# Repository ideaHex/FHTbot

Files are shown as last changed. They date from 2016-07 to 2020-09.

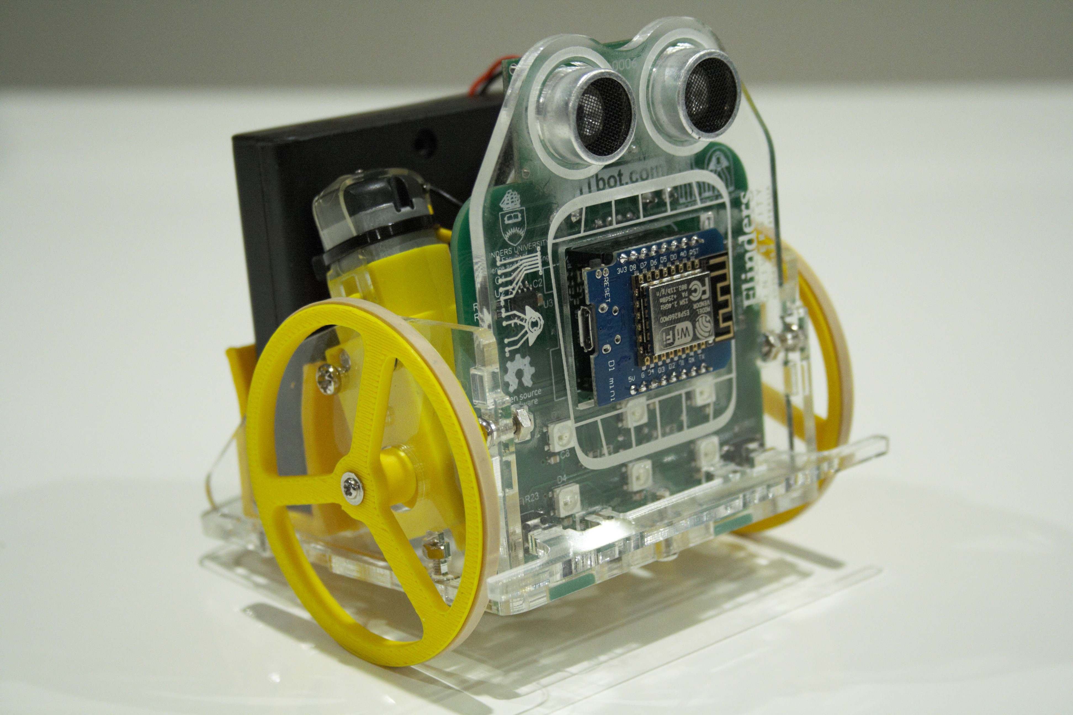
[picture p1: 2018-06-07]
FHTbot HiRes.jpg

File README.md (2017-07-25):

# FHTbot
Firmware for Makerfaire robot
<html>
  <head>

  </head>
  <body>
    <div>
      <h1><span><font face="Comic Sans MS">About</font></span></h1>
      <h3><span><br>The FHTbot was created as a result of a joint effort between Hackerspace Adelaide and Flinders University as an educational tool to provide insights into the following.<br>
<h2><span>The internet of things.</span></h2>
<ul>
  <li><span>Showing how a device can be easily set up as a secure WIFI Hotspot.</span></li>
  <li><span>Allowing most major web browsers to connect and control a real world device and take real time control over it, without the need to install 3rd party applications on the device.</span></li></ul>
<h2><span>Basic robotics.</span></h2>
<ul><li><span>Control motors.</span></li>
<li><span>Using sensors to perceive the world around it.</span></li>
<li><span>Provide visual, auditory, temperature and web client feedback.</span></li>
<li><span>A control system to give the FHTbot basic and complicated commands to perform tasks.</span></li></ul>
<h2><span>Education</span></h2><ul><li><span>
Geometry based navigation system allows students to control the FHTbot and see the FHTbot turn to the angle and proceed to the destination, put simply if you tell the but to turn right 90 degrees it will turn right, turning 180 degrees will turn and face the opposite direction.</span></li></ul>
<h2><span>Fun</span></h2><ul>
<li><span>The FHTbot was designed to be able to be driven like a remote control car.</span></li>
<li><span>The FHTbot was designed to accept a pre - programmed course.</span></li>
<li><span>The FHTbot has an assisted drive mode to help young and inexperienced drivers.</span></li></ul>
<h2><span>We all hope you have as much fun with this FHTbot as we did designing it for you.</span></h2></span></h3>
    </div>
    <br><br>
</body>
</html>

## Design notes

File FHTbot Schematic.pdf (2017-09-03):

# RIGHT_SW VCC

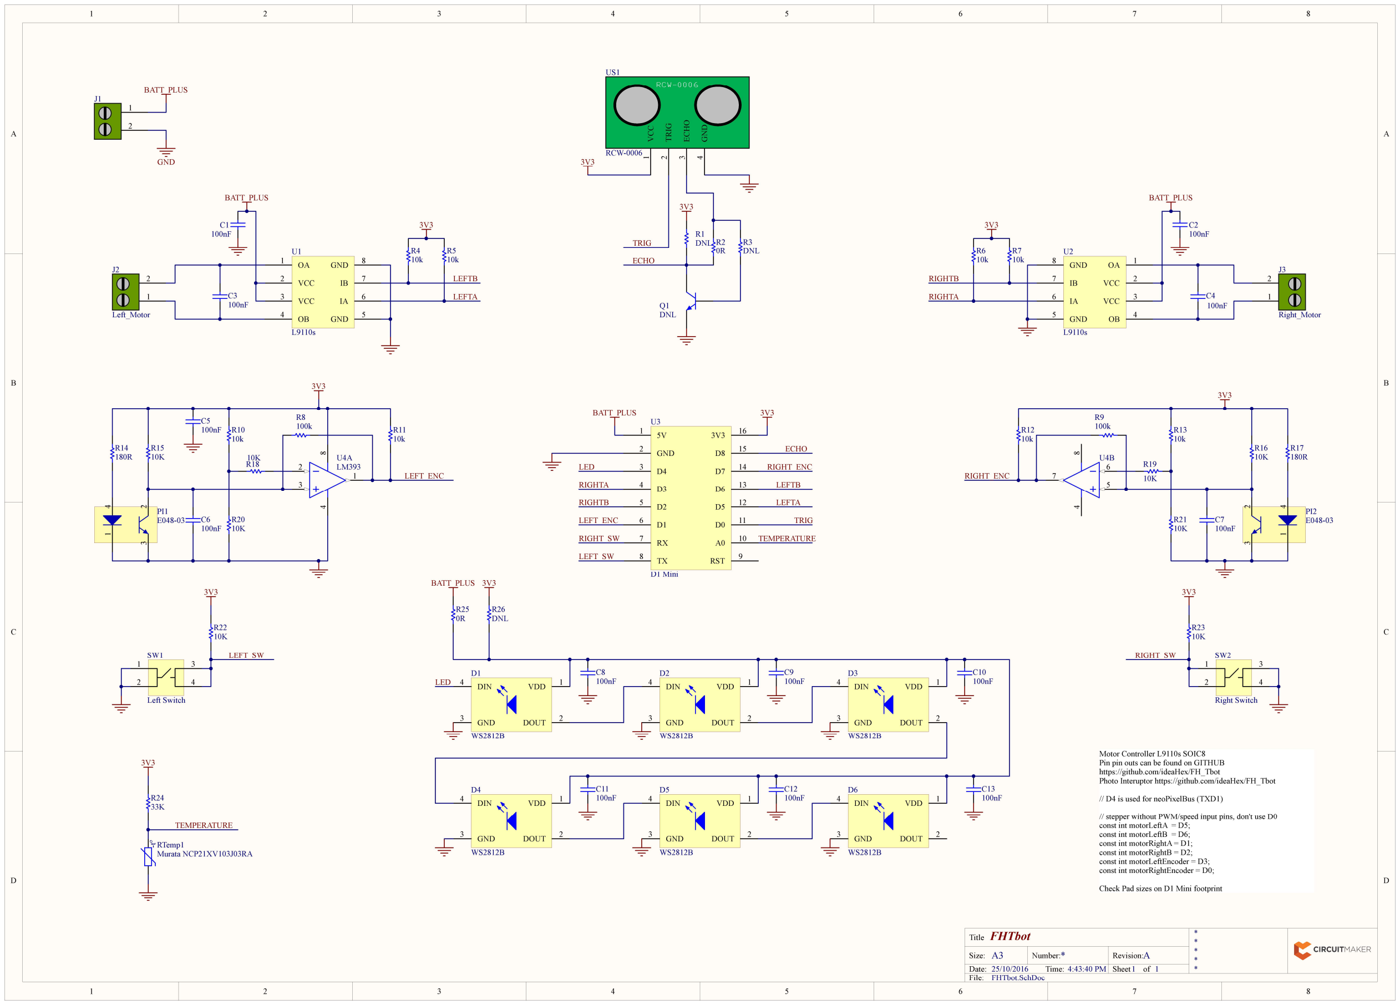
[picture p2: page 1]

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
## FHTbot

* | A
25/10/2016 | 4:43:40 PM
FHTbot.SchDoc

Title

Size: | Number:
Date:
File:

Revision:
Time: | Sheet | of

A3

VDD | 1
DOUT | 2 GND 3

DIN 4

D5

WS2812B

VDD | 1
DOUT | 2 GND 3

DIN 4

D4

WS2812B

VDD | 1
DOUT | 2 GND 3

DIN 4

D6

WS2812B

VDD | 1
DOUT | 2 GND 3

DIN 4

D3

WS2812B

VDD | 1
DOUT | 2 GND 3

DIN 4

D2

WS2812B

VDD | 1
DOUT | 2 GND 3

DIN 4

D1

WS2812B

1

2

J1

1

2

J2

Left_Motor

1

2

J3

Right_Motor

BATT_PLUS

GND

BATT_PLUS

3

2

### 1 ⁸ 4

U4A
LM393

5

6

7 8 4
U4B

R14
180R

R10
10k

R20
10K

3V3

C6
100nF

100nF

C3

C5
100nF

C8
100nF

C9
100nF

C10
100nF

C13
100nF

C12
100nF

C11
100nF

R8
100k
BATT_PLUS | 3V3

Motor Controller L9110s SOIC8
Pin pin outs can be found on GITHUB https://github.com/ideaHex/FH_Tbot
Photo Interuptor https://github.com/ideaHex/FH_Tbot

// D4 is used for neoPixelBus (TXD1)

// stepper without PWM/speed input pins, don't use D0 const int motorLeftA = D5;
const int motorLeftB = D6;
const int motorRightA = D1;
const int motorRightB = D2;
const int motorLeftEncoder = D3; const int motorRightEncoder = D0;

Check Pad sizes on D1 Mini footprint

OA | 1
VCC | 2
VCC | 3
OB | 4 GND 5

IA 6

IB 7

GND 8

U2

L9110s

OA 1

VCC 2

VCC 3

OB 4 | GND | 5
| IA | 6
| IB | 7
GND | 8

U1

L9110s

C1
100nF
BATT_PLUS | BATT_PLUS
| C2 100nF

100nF

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
Left Switch

1

2 4

3

SW2

Right Switch

R17
180R

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
100nF

R9
100k

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
3V3 | 3V3

LED

LED

3V3 | 3V3
RIGHTA | LEFTB

LEFT_ENC

LEFT_ENC

RIGHT_ENC

ECHO

TRIG

ECHO

TRIG

RIGHT_ENC

LEFT_SW | RIGHT_SW -tº RTemp1

Murata NCP21XV103J03RA

R24
33K

3V3

TEMPERATURE

TEMPERATURE

LEFTA

LEFTB

RIGHTA

RIGHTB

RIGHTB | LEFTA

R15
10K

5V 1

GND 2

D4 3

D3 4

D2 5

D1 6

RX 7

TX 8 | RST | 9
| A0 | 10
D0 | 11
D5 | 12
D6 | 13
D7 | 14
D8 | 15
3V3 | 16

U3

D1 Mini

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
LEFT_SW

### 1 TRIG

### 2 ECHO 3 GND

4

RCW-0006

US1

RCW-0006 3 2 1 4 | PI1
E048-03 | 3 2 | 1 4
PI2
E048-03

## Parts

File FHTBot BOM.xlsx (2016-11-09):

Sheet: BOM
Purchased Parts
Qty | Item | Description
2 | Motors | 48:1 Gear motor
2 | Wire | Yellow wire xx mm long
2 | Wire | White wire xx mm long
2 | Cable tie | Cable tie 100mm x 2.5mm
1 | Battery Box | Battery box for 3 x AA battery with switch
3 | Battery | AA battery
1 | Processor | WEMOS D1 mini breakout board for ESP8266EX
1 | Main Board | Assembled FHTBot PCB (see FHTBot PCB BOM for details)
1 | Ultrasonic sensor | RCW0006 Ultrasonic distance sensor, 3V compatible
1 | Velcro | 15cm Self adhesive Velcro strip
2 | Tyres | Size 63 Rubber bands
1 | Castor | M3 Dome nut
1 | Screw for castor | M3 x 6 pan screw
4 | Screw for Motors | M3 x 25 Screw
7 | Screws for Chassis | M3 x 10 Screw
11 | Nuts | M3 Hex nut
4 | Screws for wheels & Encoders | Self Tapping Machine Screw M2.3x6mm Phillip head W/Shoulder
3D Printed Parts
Qty | Item | Description
2 | Wheels | 3D Printed wheels (Wheel.stl)
Laser Cut Parts
Qty | Item | Description
2 | Side | 3 mm thick Clear Acrylic (Side v23.dxf)
1 | Base | 3 mm thick Clear Acrylic (Base v19.dxf)
1 | Front | 3 mm thick Clear Acrylic (Front v37.dxf)
2 | Encoder Spaces | 6 mm thick Acrylic (EncoderSpacer v6.dxf) or 4 @ 3mm thick
2 | Encoders | 3 mm thick Black Acrylic (EncoderWheel v15.dxf)
1 | Bumper | 3 mm thick Clear Acrylic (Bumper v17.dxf)

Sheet: PCB BOM
Designator | Qty | Description | Footprint
J1, J2, J3 | 3 | Screw Terminal
C1, C2, C3, C4, C5, C6, C7, C8, C9, C10, C11, C12, C13 | 13 | 100nF Capacitor | 0805
U1, U2 | 2 | L9110s Motor Controller IC | SOIC-8
R1, R3, R26 | 0 | Do Not Load | 0805
R2, R25, | 2 | 0R Resistor | 0805
R4, R5, R6, R7, R10, R11, R12, R13, R15, R16, R18, R19, R20, R21, R22, R23, R34 | 17 | 10K Resistor | 0805
R14, R17 | 2 | 180R Resistor | 0805
R8, R9 | 2 | 100k Resistor | 0805
RTemp1 | 1 | 33k Resistor | 0805
U3 | 1 | WEMOS D1 Mini
U4 | 1 | LM393 Comparator IC | SOIC-8
US1 | 1 | Header Female RA 4-way
Q1 | 0 | Do Not Load
PI1, PI2 | 2 | E048-03 Photo-interruptor
SW1, SW2 | 2 | Tactile Switch | 6mm x 6mm
D1, D2, D3, D4, D5, D6 | 6 | WS21182 RGB LED

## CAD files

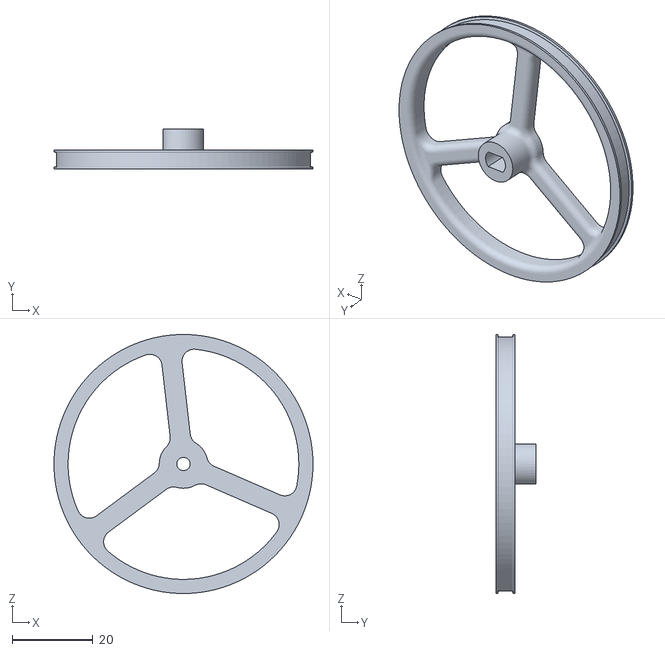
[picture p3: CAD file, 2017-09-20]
Wheel Up.stl
64.0 x 10.0 x 64.0

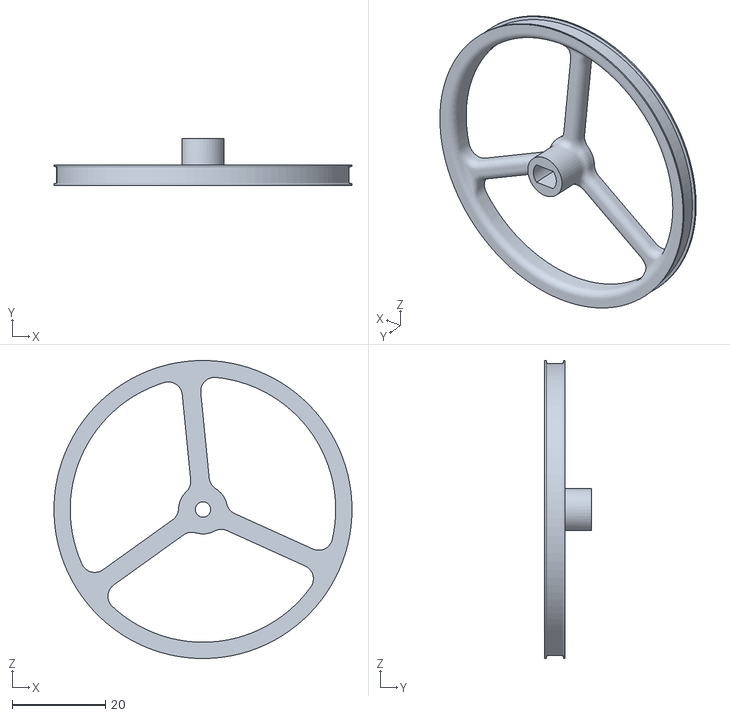
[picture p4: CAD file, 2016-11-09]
Wheel.stl
64.0 x 10.0 x 64.0

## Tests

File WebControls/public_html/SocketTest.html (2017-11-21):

# FHTbot

Touch the screen and move - works with mouse too

__ �C | | ____mm

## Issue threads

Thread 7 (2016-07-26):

Test Issue

ideaHex, 2016-07-26:
Hello World!

TildenG, 2016-07-26:
Looks good

TildenG, 2016-07-26:
I just remembered the standard ping sensor won't work consistently under 5V, I found this out the hard way !. Is there a 3.3V version ?

TildenG, 2016-07-29:
I found a mention on a blog that said that the "HC-SR04+" is a 3.3V version, however I can't find any.

ideaHex, 2016-07-29:
I purchased a IR obstacle sensor from Jaycar tonight so I will play with that as well.

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

TildenG, 2016-07-31:
I've been writing my own ping routines because I'm not happy with the slow inaccurate output from most libraries, I found that my sensor only worked when I connected the echo and trigger together on the 3.3V side of the level converter.
So far I get mm accurate results at 100 pings a second without blocking or oversampling :) .

/*
 * This is a non blocking ping example for the ESP8266 it is capable of 100 pings
 * a second with millimeter accuracy without oversampling.
 *
 * The documentation recommends not pinging faster the 60ms to avoid echo's creating
 * false readings, however I have tested at 10ms at close range (<200mm) without problems
 *
 * Trigger and echo pins need to be tied together on LV side of level converter.
 */

#define TRIGGER D6                                            // Trigger pin
volatile long pingTime;                                       // time taken to complete ping in uS
volatile int distance = -1;                                   // distance in mm

#define MAX_TEST_DISTANCE 5000                                 // in mm
byte maxTimeNeeded = (MAX_TEST_DISTANCE / 10.0 * 58) / 1000;   // in ms
unsigned long previousMillis = millis();                       // used for timeout for no ping received
byte minimumDelay = 10;                                        // to prevent false echo's

void setup() {
  Serial.begin (115200);
  pinMode(TRIGGER, OUTPUT);
}

void loop() {
    getDistance();
}

void startup(){               // ready now, wait for distance
  previousMillis = millis();
  pingTime = micros();
  detachInterrupt(TRIGGER);
  attachInterrupt(TRIGGER, calculateDistance, FALLING);
}
void calculateDistance(){
  long duration = micros() - pingTime + 50;  // added 50 uS to calibrate sensor
  distance = (duration/2.0) / 29.1 * 10.0;
 // distance = (max((duration + 57 / 2) / 57, (duration ? 1 : 0)));
}
void triggerPing(){
  detachInterrupt(TRIGGER);
  pinMode(TRIGGER, OUTPUT);

  digitalWrite(TRIGGER, LOW);         // start low
  delayMicroseconds(2);

  digitalWrite(TRIGGER, HIGH);        // datasheet states a uS 10  pulse to start
  delayMicroseconds(10);

  digitalWrite(TRIGGER, LOW);
  pinMode(TRIGGER, INPUT);            // set input to output so only 1 pin is needed

  attachInterrupt(TRIGGER, startup, RISING);
}

int getDistance(){                   // returns distance or -1 if not available
  if (distance != -1 && millis() - previousMillis > minimumDelay){
      Serial.printf("Distance: %d mm \r\n", distance);
      distance = -1;
      triggerPing();
    }

    if (millis() - previousMillis > maxTimeNeeded){
      previousMillis = millis();    // to stop false starts
      distance = -1;
      triggerPing();
    }
    return distance;
}

TildenG, 2016-08-03:
It would appear that if an hardware interrupt is triggered during a client connect or other client functions, the client locks up ALL wifi functions effectively disconnecting the wifi !!!.
See https://github.com/esp8266/Arduino/issues/1020 for more info, this may cause issues with the ping sensor and encoder wheel !!!.

As a hack we may be able to use the hardware serial(UART) for the ping.

ideaHex, 2016-08-05:
I am in the process of testing. UART0 can be "swapped" to D7 & D8 this may let us use this for the US100 sensor without removing it to program. call "Serial.swap();" after the Serial.Begin.

The Adafruit Neopixel library should be able to use any pin to drive the LEDs. We still need then to work out encoders.
I will continue to play!

TildenG, 2016-08-06:
I've been testing the neopixel library on TXD1 (D4) and it works fine (NeoPixelBus<NeoGrbFeature, NeoEsp8266Uart800KbpsMethod> strip(6, D4);), so no problem there, I was thinking of using a couple mosfets to isolate one of the pins on the US100 so we can leave it on the default TX and RX which will free up a couple of GPIO pins, though your option is better for debugging.
In the last update I was able to remove the blocking code that waited for each client request to close, which removed about a 85mS pause on each receive :), so A software detect on the encoders may work, but I don't know how accurate it will be until we test it.
I've considered using an ATTiny85 or ATMEGA328p-au to process the data from the US100 and encoders but would add about $1.50 to each bot !.
I won't be able to make it in this Tuesday, but I'll put pull requests through if I get any coding done.

How are you going to include the neopixel library with the project to make it easy for users to install and use ?

ideaHex, 2016-08-06:
Can we use a timer interrupt with out breaking Wifi? We could then just pole the encoder pins in the interrupt as long as the time interval is faster than the encoders which I don’t expect to be real fast anyway.

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

TildenG, 2016-08-06:
I was thinking of just polling the encoder in the main loop, I'll do some tests either tomorrow or Monday, there is one hardware timer, not sure if it will effect wifi, in the documentation it relates to software timers too, like we used with ticker, given that the slot is about 1mm wide and its 40 pulses per revolution, max rpm 100, so 4000 per minute, 12000 per minute allowing for the space between high and low, should be easy, and in a pinch we can set cpu to 160mhz if it's just under.

TildenG, 2016-08-07:
ok so the results are in:
I started the test after the client connected so the timing would include 10 packets per second, I also changed each led to random colors(all 6) with each packet, I added an extra read for 2 pins to emulate the encoders on each loop for maximum delay.
At 80 MHZ I get 2372835 loops per minute,
At 160 MA I get 4658326 loops per minute.
so unless we add blocking functions I'd say where fine :)

TildenG, 2016-08-17:
**This should help with pin selection.**

GPIO 16, D0 no PWM or interrupts.

GPIO 0,   D3**(FLASH)** must start high to run , low to program.
GPIO 15, D8**(TXD2)** must start low.
GPIO 2,   D4**(TXD1)** when low will illuminate built in led - pulses during upload, some articles say it needs to be high to start, I guess that's why the led is connected as a pull up.

GPIO 5,   D1 Clear
GPIO 4,   D2 Clear
GPIO 14, D5 Clear
GPIO 12, D6 Clear
GPIO 13, D7 Clear

GPIO 3 -  RX**(RXD0)**
GPIO 1 -  TX**(TXD0)**

TildenG, 2016-08-17:
I've looked at a couple of optical encoders, side by side they will increase the width of the bot by about 16mm, we could rotate one 180 degrees, but I don't think it would look nice.

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

TildenG, 2016-09-07:
I have noticed that sometimes when the bot stops, one of the encoders led's is flickering, sending false steps to the microcontroller, I'm assuming its right on the cusp of triggering the comparator, any thoughts on a hardware solution for this ?

ideaHex, 2016-09-07:
Might have to fine tune the comparator circuit.

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

TildenG, 2016-09-13:
We need to look into gzip to transmit web pages
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
TildenG, 2016-09-22:
@Rodinga  After a couple of refreshes it came up, could you expand it to full width ?
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

Rodinga, 2016-09-26:
I've modified to CSS to widen it. It'll come forward with everything once I sort out bot commands.

TildenG, 2016-09-26:
The last update improves the cache, and I've improved the headers for the other packets.

The Turtlemode page usually load's on the first try or first refresh so, much better than before.

Currently the drive mode is acting strange on IE, but seems fine on the other browsers I've tested.

I'm about halfway through the encoder - motor rewrite.

I'll do another upload tonight.

If anybody could test the new code on there phone(Including uploading to the SPIFFS or it will break)  that would be great.

TildenG, 2016-09-28:
I just done some quick current tests on the esp8266 D1 mini with nothing attached and at 80 MHZ and 160 MHZ.

At 80 MHZ the average current draw was about 83.5 mA at 5V side.

At 160 MHZ the average current draw was about 88 mA at 5V side.

These are very rough figures as I haven't compensated for voltage drop across all the extra leads and the poor connection I get from alligator clips, but around 5 mA sounds about right as the cpu is only a small portion of the total current consumed by the D1.

ideaHex, 2016-09-28:
Problem with Ultra-sonic sensors:( US-100 are not coming but I have received a refund from ebay. All the other US-100 are around $4 each. Can we use RCW-0006? https://www.aliexpress.com/item/RCW-0006-Ultrasonic-Ranging-Module-3-0V-5-5V-beyond-HC-SR04-30498/32614447324.html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,searchweb201602_3_10057_10065_10056_10068_10037_10055_10054_10069_301_10059_10033_10058_10032_418_10073_10017_10070_10060_10061_10052_10062_10053_10050_10051,searchweb201603_6&btsid=b633f4cf-f04c-4bd5-b51b-b48deae905e5
Seems to be 3V and compatible with HCR-04. Price is good just need to make sure I can them in a timely manner.

TildenG, 2016-09-28:
We might be able to connect the trigger to D0 and echo on D8, if the echo is floating when the unit powers up.  We could then enable the interrupt on D8. The timing and the rest of the spec's look about right, I'd have to double check.

Wouldn't know until we plug it in.

TildenG, 2016-09-29:
Ok, I've read the info on the link to the RCW-0006, the english is really bad, I can only guess at this stage but it appears to use the same protocol as the SCR-04 and US-100.

 **No temperature output !.**

The trigger pin looks to have a pull up on it so it can't be joined to the echo pin and connected to D8 directly, maybe with a little trial and error a resistor could be placed between echo & trigger. However we still have D0 open so we can use that to trigger the RCW-0006.

Normal operation of the RCW-0006 shows the echo high only when it's waiting for a return signal, but there is no info on its state at startup, if it's high the ESP8266 won't boot.

@ideaHex  have you ordered them ?

ideaHex, 2016-09-29:
Not yet. That was tonight's project. I will digest your comments tonight.

ideaHex, 2016-09-29:
OK ordered RCW-0006 hopefully will get them in time. Paid extra to get them in 14 days.
So can we use D0 as Trigger and D7 as echo? Should be able to isolate pins with transistors etc if required.
I have received D1 minis, Batteries, Motors, Motor controller ICs, Screw terminals, LEDs, Photo interrupters,  screws, battery holders, cable ties.
I think I'm close to finishing wheels.
Just need some small parts for PCB should be able to get them from Element 14 or RS.
Now just need to finish/start PCB.

TildenG, 2016-09-30:
D0 for trigger because it doesn't support  interrupts and is doesn't matter if it's high or low, **_D8_** because the encoder is on D7, D8 must be low for the esp8266 to start.

 If we had one to test to see if the echo is low when it powers up that would be perfect.

I suppose we could invert the echo pin with a transistor and a pull down resistor if its a problem. Would a PNP transistor or a P channel- fet work ok in this situation ?.

I could tweek the code that I wrote for the US-100 using interrupts , just invert the triggers and split up the trigger/echo pins in the code.

This kind of ping sensor will cost us 10 uS per trigger, shouldn't impact on performance.

ideaHex, 2016-09-30:
I'm going to take a look at the schematic in detail over the next few days. I'll get you to check it out when ready. I might then try and etch a prototype PCB.

TildenG, 2016-10-05:
@Rodinga , I've tested the turtlebot mode on safari, I get no heartbeat
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

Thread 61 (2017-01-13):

Add robot functions in turtle mode

ideaHex, 2017-01-13:
It would be good to be able to add more blocks to turtle mode. Some that jump to mind would be:
Bumper state
distance from object using ultrasonic sensor
a delay or wait a certain time
Control the LEDs
Battery voltage

TildenG, 2017-01-13:
And play tune.

Rodinga, 2017-01-13:
I'll start putting some thought into implementation. Bumper for example might be more of a broadcasted event rather than a state. Or we sample so fast that blockly just keeps checking until there is a depressed state. Or we can do both.

On 13 Jan. 2017 5:04 pm, TildenG <notifications@github.com> wrote:

And play tune.

—
You are receiving this because you are subscribed to this thread.
Reply to this email directly, view it on GitHub<https://github.com/ideaHex/FHTbot/issues/61#issuecomment-272372040>, or mute the thread<https://github.com/notifications/unsubscribe-auth/ASkC_7hT8W5WYOWoXw_Bpl_z_hahd3iiks5rRxsPgaJpZM4Lii86>.

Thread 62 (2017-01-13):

PCB update

ideaHex, 2017-01-13:
Update the PCB. Improvements should include:
Allow robot to run from higher voltage minimum 4 AA batteries
Measure battery voltage in place of temperature
Allow safe connection of USB without turning off battery pack

ideaHex, 2017-01-13:
Should we stick with D1 mini or update to D1 mini Pro

D1 Mini 4M Flash, CH340G USB 2 Uart chip, $5.42ea
D1 Mini Pro 16M flash, CP2104  USB 2 Uart chip, $6.77ea

They are both the same size and are based on the ESP8266EX so perhaps they would be interchangeable.

ideaHex, 2017-01-13:
Should we stick with a combination through hole and surface mount or just through hole?

TildenG, 2017-01-13:
Does the D1 Mini Pro have an antenna on board, the version I looked at only had an antenna jack, and didn't mention how the flash memory was laid out ? 1MB program, 15MB SPIFFS ???.
Extra flash memory is always nice.

TildenG, 2017-01-13:
As far as through hole is concerned, its up to what the end user wants, if they want to reconfigure the bot, through hole all the way, or else surface mount.

ideaHex, 2017-01-13:
D1 mini pro has built in ceramic antenna and option for external antennae.

TildenG, 2017-01-13:
Currently the main program uses 290KB of the 1MB program memory, so plenty of room left there and about 790KB of the 3MB SPIFFS, so plenty of room there too.

ideaHex, 2017-01-13:
Ok Will stick with D1 mini.

ideaHex, 2017-05-16:
Forked FHTbot on Circuit maker Now FHTbot - V2.

ideaHex, 2017-08-01:
Connect LEDs directly to batteries
Use level converter from BSS138 MOSFET to drive signal
Increase C1 & C2 Motor controller Decoupling Capacitors
Add Capacitor after diode on 5V input to WEMOS

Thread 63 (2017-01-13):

"School Proof" chassis

ideaHex, 2017-01-13:
Design new chassis the would be suitable for a School class room.

Some options:
Change material from acrylic to Acetal
3D printed chassis

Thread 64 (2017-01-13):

Improve Encoder design

ideaHex, 2017-01-13:
Work on tryig to improve the resolution of the encoder wheels. This could include making more holes and/or increasing the size of the wheel.

TildenG, 2017-08-23:
Where now at the point of diminishing returns, if we increase the resolution, the wheel slip is enough to counter any more gain.
We should close this issue.

Closed 2017-08-23.

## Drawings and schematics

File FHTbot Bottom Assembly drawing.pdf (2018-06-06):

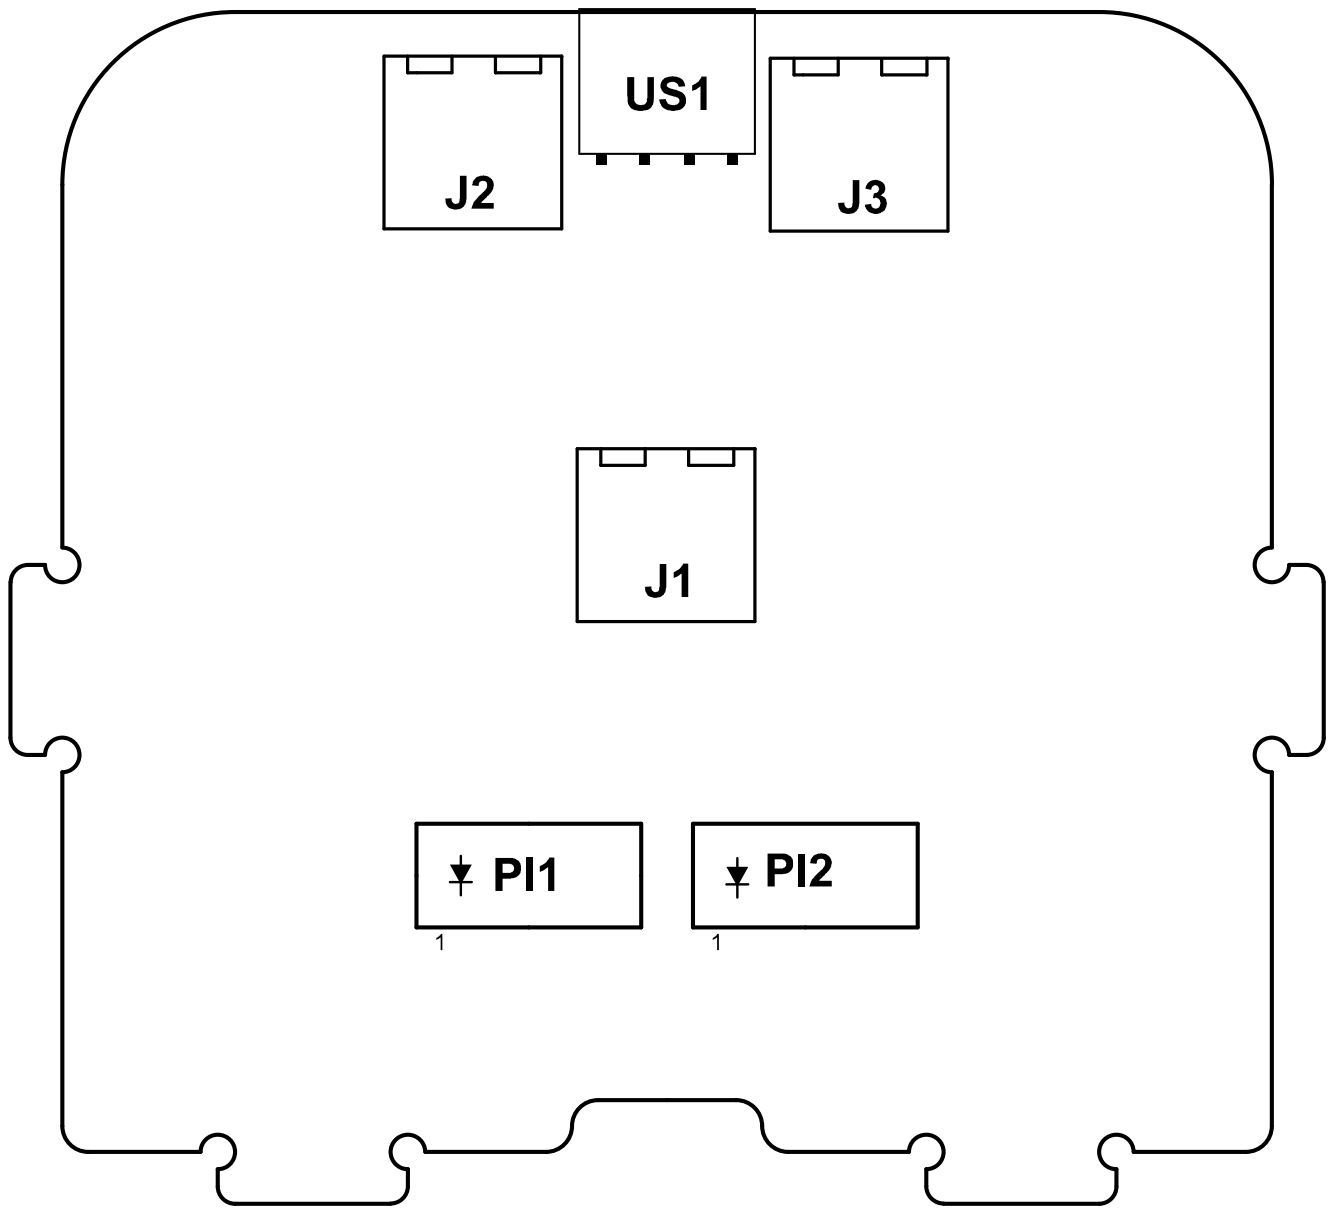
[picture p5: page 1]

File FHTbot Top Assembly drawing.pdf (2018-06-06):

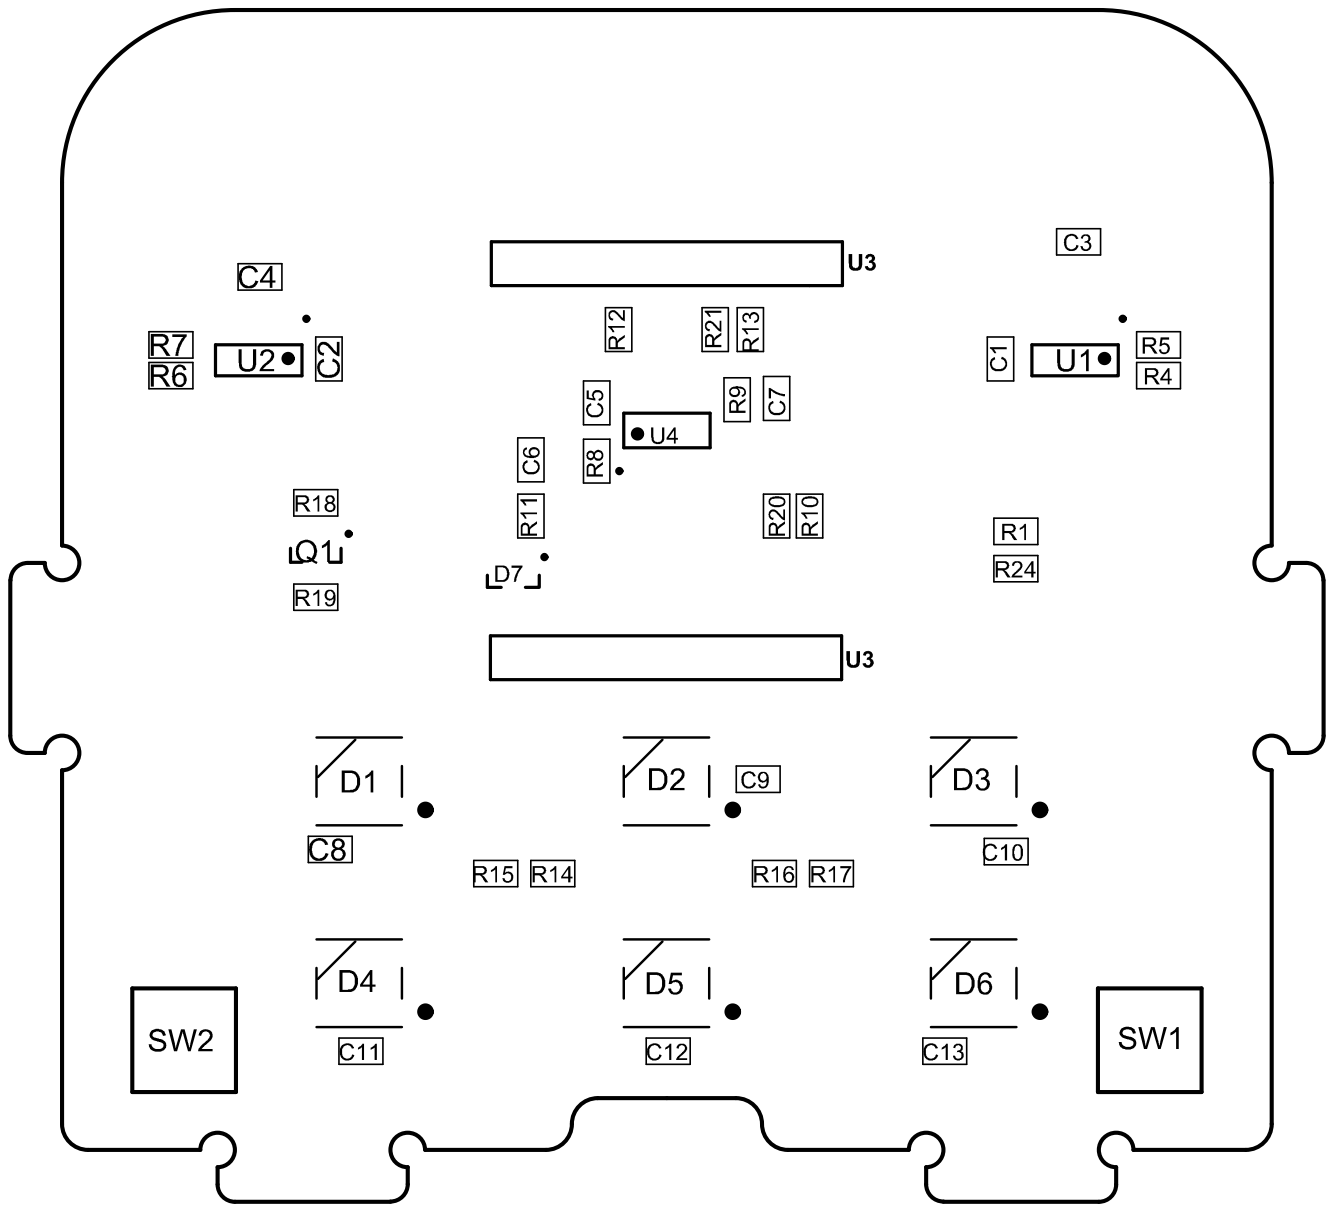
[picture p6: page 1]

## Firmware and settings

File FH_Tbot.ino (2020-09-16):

/*
Copyright 2017, Tilden Groves, Alexander Battarbee.

Licensed under the Apache License, Version 2.0 (the "License");
you may not use this file except in compliance with the License.
You may obtain a copy of the License at

    http://www.apache.org/licenses/LICENSE-2.0

Unless required by applicable law or agreed to in writing, software
distributed under the License is distributed on an "AS IS" BASIS,
WITHOUT WARRANTIES OR CONDITIONS OF ANY KIND, either express or implied.
See the License for the specific language governing permissions and
limitations under the License.
*/

#pragma GCC optimize("-O2") // O0 none, O1 Moderate optimization, 02, Full
                            // optimization, O3, as O2 plus attempts to
                            // vectorize loops, Os Optimize space
#include "EncoderMotorControl.h"
#include "FlashFiles.h"
#include "NeoPixelAnimations.h"
#include "RCW0006Ping.h"
#include "botVoltage.h"
#include <DNSServer.h>
#include <ESP8266WiFi.h>
#include <ESP8266WebServer.h>
#include <FS.h>
#include <NeoPixelBus.h>
#include <Ticker.h>
#include <WebSockets.h>
#include <WebSocketsClient.h>
#include <WebSocketsServer.h>

extern "C" {
#include "user_interface.h"
}

//////////////////////
// WiFi Definitions //
//////////////////////

const char *password = "12345678"; // This is the Wifi Password (only numbers
                                   // and letters,  not . , |)
String AP_Name = "FHTBot"; // This is the Wifi Name(SSID), some numbers will be
                           // added for clarity (mac address)
bool enableCompatibilityMode = false; // turn on compatibility mode for older
                                      // devices, specifically sets no
                                      // encryption and 11B wifi standard

void Stop(void);
void CheckHeartBeat(void);
void setupWiFi(void);
void setupWebsocket(void);
void initHardware(void);
void sendFile(String);
String getContentType(String);
void updateMotors();
void testBumper();
void leftBumperHitFunction();
void leftBumperReset();
void rightBumperHitFunction();
void rightBumperReset();
void checkAutoMode();
void checkBoredBot();
void motorLeftEncoderInterruptHandler();
void motorRightEncoderInterruptHandler();
void updateClient();
void updateMotorSpeed(void);
void feedback();
void handleSounds();
void handleRoot();
void handleNotFound();
void handleHeartBeat();
void handleRecievedPacket();
void WSRequest(String req, int clientNum);
void webSocketEvent(uint8_t num, WStype_t type, uint8_t *payload,size_t payLength);

/////////////////////
// Pin Definitions //
/////////////////////

// D4 is used for neoPixelBus (TXD1)
// D0 is used to trigger ping
// D8 is used for echo of ping
#define D9 3 // D9 & D10 aren't defined so define them here
#define D10 1
const int motorLeftA = D6;
const int motorLeftB = D5;
const int motorRightA = D2;
const int motorRightB = D3;
const int motorLeftEncoder = D7;
const int motorRightEncoder = D1;
const int leftBumper = D9;
const int rightBumper = D10;

encoderMotorController motors(motorLeftA, motorLeftB, motorRightA, motorRightB,
                              motorLeftEncoder, motorRightEncoder);
Ticker motorControllerTicker;
Ticker tempTicker;
Ticker lBH; // left bumper hit reverse timer
Ticker rBH; // right bumper hit reverse timer
ESP8266WebServer server(80);
WebSocketsServer webSocket = WebSocketsServer(81);
DNSServer dnsServer;
Ticker HeartBeatTicker;
int distance = 500;
boolean driverAssist = false;
bool HeartBeatRcvd = false;
String closeConnectionHeader = "";
boolean pingOn = false;
unsigned long nextBoredBotEvent = 0;
int boredBotTimeout = 60000;             //in ms
boolean boredBotRunning = false;		// in middle of bored bot function
boolean leftBumperHit = false;
boolean rightBumperHit = false;
boolean autoMode = false; // drive mode with no client connected
unsigned long autoModeNextUpdate = 0;
unsigned long autoModeNextEvent = 0;
//#define Diag                           // if not defined disables serial communication after initial feedback
long timerPing;
short updateRound = 0;


void Stop(){
  motors.manualDrive(0,0);
  if (!boredBotRunning)setColor(RgbColor(0,0,0));// turn off LED's to save power
  pingOn = false;                        // turn off ping to save power
  driverAssist = false;
}

void CheckHeartBeat(){
	updateMotorSpeed(); 				// check battery level and adjust speed
  if (HeartBeatRcvd == true)
  {
    HeartBeatRcvd = false;
    nextBoredBotEvent = millis() + boredBotTimeout; // reset bored bot timer
  } else {
    Stop();
  }
}

void setup(){
  system_update_cpu_freq(80);           // set cpu to 80MHZ or 160MHZ !
  system_phy_set_max_tpw(82); 			    // 0 - 82 radio TX power
  setupWiFi();
  setupWebsocket();
  initHardware();
  HeartBeatTicker.attach_ms(991, CheckHeartBeat);
  closeConnectionHeader += F("HTTP/1.1 204 No Content\r\nConnection: Close\r\n\r\n");
  nextBoredBotEvent = millis() + boredBotTimeout;
}

void loop(){
  // time dependant functions here
  checkBoredBot();
  checkAutoMode();
  if (pingOn) {
    getDistance(); // ping pulse/update function must be called to ping
    distance = getMedian();
    if (driverAssist) {
      if (distance < 200) { // too close bounce back
        setColor(RgbColor(255, 0, 0));
        motors.manualDrive(0, 500);
      }
    }
  }

  if (driverAssist) {
    testBumper();
  }
   dnsServer.processNextRequest();      // update DNS requests

  //Loop WebSocket Server
  webSocket.loop();
  // handle client requests
  server.handleClient();
  
  if(motors.updateSoundPlayer()) HeartBeatRcvd = true; // non - blocking sounds
}
/**
 * A faster version of exeReq for websockets.
 * Features WS response and a shorter command list.
 */
void WSRequest(String req, int clientNum) {
  // Empty request tripwire
  if (!req.length()) {
    // empty request
    return;
  }
  HeartBeatRcvd = true;
  if (req.indexOf("/HB") != -1) {
    // Fast Catch and Release, HB handled above.
    updateClient();
    yield();
    return;
  }
  // Serial.println("\r\n" + req);
  int indexOfX = req.indexOf("/X");
  int indexOfY = req.indexOf("/Y");
  if (indexOfX != -1 && indexOfY != -1) {
    pingOn = true;
    int indexOfHB = req.indexOf("/DA");
    if (indexOfHB != -1){
      driverAssist = true;
      }
    if (req.indexOf("/DM") != -1){
      driverAssist = false;
      }
    yield();
    String xOffset = req.substring(indexOfX + 2, indexOfX + 8);
    int dX = xOffset.toInt();
    String yOffset = req.substring(indexOfY + 2, indexOfY + 8);
    int dY = yOffset.toInt();
    #ifdef Diag
    Serial.println("dX"+String(dX)+"dY"+String(dY));
    #endif
    // driver assist
    if (driverAssist) {
      updateBlinkers(dX, dY);
      if (distance < 450 && distance > 199 && dY < 0) {
        setColor(RgbColor(90, 105, 95));
        motors.hardRightTurn();
        dX = 500;
        dY = -100;
      }
      if (distance < 200) {
        setColor(RgbColor(255, 0, 0));
        dY = 500;
      }
    } else {
      pixelTest();
    }
    motors.manualDrive(dX, dY);
    updateClient();
  }else{
    //TODO REVIEW THESE FOR FALSE ACTIVATION LS PROVED TO HIT
  if (req.indexOf("data,") != -1) {
    yield();
    req.remove(0, req.indexOf("data,"));
    req.trim();
    motors.startCommandSet(req);
    return;
  }
  if (req.indexOf("save,") != -1) {
    //File pushed by turtle mode to be saved
    //save,fileName,xmlstring
    #ifdef Diag
    Serial.println("Save Request:" + req);
    #endif
    String dataString = req.substring(req.indexOf(","));
    int titleComma = dataString.indexOf(",");
    String fileName = "/T/" + dataString.substring(0,titleComma);
    File dataFile = SPIFFS.open(fileName,"w");
    if(dataFile){
      //Write to file
      dataFile.print(dataString.substring(titleComma));
      dataFile.close();
      //respond to client
      webSocket.sendTXT(clientNum, "File Saved Successfully");
    }else{
      #ifdef Diag
      Serial.println("Failed to create file");
      #endif
      //respond to client
      webSocket.sendTXT(clientNum, "Failed to create file. May already exist.");
    }
  }
  //Listing directory contents
  if(req.indexOf("ls,")!= -1){
     //load dir object
     Dir dir = SPIFFS.openDir(req.substring(req.indexOf(",")));
     String out = "";
     while(dir.next()){
      File f = dir.openFile("r");
      //Compiling comma delimited list of file names
      out += dir.fileName();
     }
     #ifdef Diag
     Serial.println("output:" + out);
     #endif
     webSocket.sendTXT(clientNum, out);
  }
  }
}

/**
 * Handles Websocket reception, deciding what needs to be done vs the type of
 * message.
 */
void webSocketEvent(uint8_t num, WStype_t type, uint8_t *payload,
                    size_t payLength) {

  #ifdef Diag
  Serial.println("WEBSOCKET EVENT");
  Serial.println(millis() - timerPing);
  #endif
  timerPing = millis();
  switch (type) {
  case WStype_DISCONNECTED: {
    // perform disconnection events (i.e. send bot to idle.)
    #ifdef Diag
    IPAddress ip = webSocket.remoteIP(num);
    Serial.println(String(num) + " Client from " + ip[0] + "." + ip[1] + "." + ip[2] + "." + ip[3] + " Has Disconnected " + "\n");
    #endif
    // Stop Bot
    Stop();
  } break;
  case WStype_CONNECTED: {
    // HANDLE NEW CLIENT CONNECTION
    #ifdef Diag
    IPAddress ip = webSocket.remoteIP(num);
    Serial.println(String(num) + " Connected from " + ip[0] + "." + ip[1] +
                   "." + ip[2] + "." + ip[3] + " url: " + String(*payload) +
                   "\n");
    #endif
    // ACK connection to client
    webSocket.sendTXT(num, "Connected to FH_Tbot");
  } break;
  case WStype_TEXT: {
    // Perform actions based on a good payload.
    #ifdef Diag
    Serial.println("Starting charstream to char array conversion");
    #endif
    char A[payLength + 1];
    char *strncpy(char *A, const char *payload, size_t payLength);
    A[payLength] = '\0';
    String b((char *)payload);
    #ifdef Diag
    Serial.println(String(num) + "get Text: " + b +
                   " length: " + String(payLength) + "\n");
    #endif
    HeartBeatRcvd = true;
    WSRequest(b, num);
    // Feedback
  } break;
  }
}

void setupWiFi(){
  Serial.begin(115200);
  WiFi.mode(WIFI_AP);

  // Create a unique name by appending the MAC address to the AP Name

  //AP_Name = AP_Name + " " + WiFi.softAPmacAddress();
  char AP_NameChar[AP_Name.length() + 1];
  AP_Name.toCharArray(AP_NameChar, AP_Name.length() + 1);

  /*
   * struct softap_config {
      uint8 ssid[32];
      uint8 password[64];
      uint8 ssid_len;
      uint8 channel; // support 1 ~ 13
      uint8 authmode; // Don’t support AUTH_WEP in SoftAP mode
      uint8 ssid_hidden; // default 0
      uint8 max_connection; // default 4, max 4
      uint16 beacon_interval; // 100 ~ 60000 ms, default 100
    };
   */
  // setup AP, start DNS server, start Web server

  int channel = random(1, 13 + 1); // have to add 1 or will be 1 - 12
  const byte DNS_PORT = 53;
  IPAddress subnet(255, 255, 255, 0);
  IPAddress apIP(192, 168, 1, 1);
  WiFi.softAPConfig(apIP, apIP, subnet);
  if (enableCompatibilityMode) {
    wifi_set_phy_mode(PHY_MODE_11B); // Note: ESP8266 soft-AP only support bg.
    const char *pw = "";
    WiFi.softAP(AP_NameChar, pw, channel, 0);
  } else {
    wifi_set_phy_mode(PHY_MODE_11N);
    WiFi.softAP(AP_NameChar, password, channel, 0);
  }
  dnsServer.setErrorReplyCode(DNSReplyCode::NoError);
  dnsServer.start(DNS_PORT, "*", apIP); // default FHTbot.com  //must use '.com,
                                        // .org etc..' and cant use '@ or _
                                        // etc...' ! . Use "*" to divert all
                                        // **VALID** names
	server.on("/", handleRoot);
    server.on("/Sounds", handleSounds);
	server.onNotFound(handleNotFound);
	server.on("/HB", handleHeartBeat);
	server.begin();
}

void setupWebsocket() {
  // start websocket
  #ifdef Diag
  Serial.println("Establishing Websocket Server");
  #endif
  webSocket.begin();
  webSocket.onEvent(webSocketEvent);
}

void initHardware(){
  Serial.println(F("\r\n"));
  Serial.println(F("            FHTbot Serial Connected\r\n"));
  Serial.println(F("\r\n         Disable any form of assisted WIFI\r\n"));
  Serial.print(F("\r\n  Your FHTbot Wifi connection is called "));
  Serial.println(AP_Name);
  Serial.print(F("\r\n  Your password is "));
  Serial.println(password);
  Serial.println(F("\r\n  Type FHTbot.com into your browser after you connect. \r\n"));
  SPIFFS.begin();
  delay(200);
  #ifndef Diag
    Serial.end(); // disable serial interface
  #endif
  pingSetup();
  strip.Begin();
  strip.Show();
  smile();
  // setup motors and encoders
  attachInterrupt(motorLeftEncoder, motorLeftEncoderInterruptHandler , CHANGE);
  attachInterrupt(motorRightEncoder, motorRightEncoderInterruptHandler , CHANGE);
  motorControllerTicker.attach_ms(motors.updateFrequency, updateMotors);  // attach motor update timer
 #ifndef Diag
    pinMode(leftBumper, INPUT_PULLUP);
    pinMode(rightBumper, INPUT_PULLUP);

	if (digitalRead(leftBumper) == LOW){// test for startup auto mode
		autoMode = true;
		motors.playCharge();
		autoModeNextUpdate = millis()+300;
		autoModeNextEvent = millis() + random(10000,30000);
	};
    attachInterrupt(leftBumper, leftBumperHitFunction , FALLING);
    attachInterrupt(rightBumper, rightBumperHitFunction , FALLING);
 #endif
 Stop(); 							// incase of reset, stop motors !
 resetVoltageFilter();				// setup voltage filter for first samples
}
ICACHE_RAM_ATTR void leftBumperHitFunction(){
  if (!leftBumperHit){
    lBH.once_ms(1500,leftBumperReset);
  }
  leftBumperHit = true;
}
 void leftBumperReset(){
  leftBumperHit = false;
}
ICACHE_RAM_ATTR void rightBumperHitFunction(){
  if (!rightBumperHit){
    rBH.once_ms(1500,rightBumperReset);
  }
  rightBumperHit = true;
}
void rightBumperReset() { rightBumperHit = false; }

ICACHE_RAM_ATTR void motorLeftEncoderInterruptHandler() { motors.takeStep(0); }
ICACHE_RAM_ATTR void motorRightEncoderInterruptHandler() { motors.takeStep(1); }

void updateMotors() { motors.update(); }


void checkBoredBot(){
    if (millis() > nextBoredBotEvent){       					// bored bot event called here
          nextBoredBotEvent = millis() + boredBotTimeout * 0.5; // reset bored bot timer
          // different events to be put here
          int events = 4;
          int pickedEvent = random(1,(events+1));
		  boredBotRunning = true;
          switch(pickedEvent){

    case 1: // play vroom and bright light
      setColor(RgbColor(80, 80, 80));
	  delay(20);
	  setColor(RgbColor(80, 80, 80));
      motors.playVroom();
	  boredBotRunning = false;
      break;

    case 2: // random colors
      for (int a = 0; a < 50; a++) {
        pixelTest();
        delay(25);
      }
	  boredBotRunning = false;
      break;

    case 3: // blinker rotation
      for (int a = 0; a < 4; a++) {
        delay(100);
        updateBlinkers(0, -1);
        delay(100);
        updateBlinkers(60, -1);
        delay(100);
        updateBlinkers(0, 1);
        delay(100);
        updateBlinkers(-60, -1);
      }
	  boredBotRunning = false;
      break;

    case 4: // smile
      smile();
	  boredBotRunning = false;
      break;
    }
  }
}

void testBumper(){
    #ifndef Diag
    if (!leftBumperHit && rightBumperHit){
          motors.manualDrive(-250,500);
		  motors.manualDrive(-250,500);
          motors.hardLeftTurn();
    }
    if (!rightBumperHit && leftBumperHit){
          motors.manualDrive(250,500);
		  motors.manualDrive(250,500);
          motors.hardRightTurn();                               // in reverse right becomes left
    }
     if (rightBumperHit && leftBumperHit){
          motors.manualDrive(0,500);
		  motors.manualDrive(0,500);
    }
     #endif
}

void checkAutoMode(){
	if (autoMode){
		HeartBeatRcvd = true;
		pingOn = true;
		driverAssist = true;
		int dX = -1;
		int dY = -430;
		unsigned long batteryTimeOffset = motors.getBatteryLevel() * 62;
		if (millis() > autoModeNextUpdate){
			updateBlinkers(dX,dY);
			autoModeNextUpdate = millis() + 500;
			if (leftBumperHit || rightBumperHit)autoModeNextUpdate = millis() + 2000;
			if (distance < 460 && distance > 199 && dY < 0){
				setColor(RgbColor(90,105,95));
				motors.hardRightTurn();
				dX = 500;
				dY = -50;
				autoModeNextUpdate = millis() + 1500 + batteryTimeOffset;
			}
			if (distance < 200){
				setColor(RgbColor(255,0,0));
				dY = 500;
				autoModeNextUpdate = millis() + 1200;
			}
			motors.manualDrive(dX,dY);
		}
		if (millis() > autoModeNextEvent){
			autoModeNextEvent = millis() + random(10000,30000);
			setColor(RgbColor(30,105,35));
			motors.hardRightTurn();
			dX = 500;
			dY = -100;
			motors.manualDrive(dX,dY);
			autoModeNextUpdate = millis() + 1500 + batteryTimeOffset;
			//String data = "data,L,120,";
			//motors.startCommandSet(data);
		}
	}
}
/**
 * Updates websocket client with distance/temperature information.
 * TODO CHANGE TO CHAR ARRAY
 */
void updateClient() {

  String s = "/V";
  s.concat(getCurrentVoltage());
  s.concat(",/B");
  s.concat(motors.getBatteryLevel());
  s.concat(",/D");
  s.concat(distance);
  webSocket.sendTXT(0, s);
  #ifdef Diag
  Serial.println("Return Message: " + s);
  #endif
}

void updateMotorSpeed(){
				updateVoltage();
                float voltage = getCurrentVoltage();
				motors.updateMotorSpeed(voltage);
}

// server callbacks

void handleRoot(){
	handleRecievedPacket();
	sendFile(server.uri(),&server);
}

void handleNotFound(){
	//handleRecievedPacket();
	sendFile(server.uri(),&server);
}

void feedback(){
			  float voltage = getCurrentVoltage();
              int batteryLevel = motors.getBatteryLevel();
              String s,h;
              s = F("<!DOCTYPE HTML><html><head><meta http-equiv='refresh' content='1'></head><body><script>");
              s += (";var volt=");
              s += voltage;
              s += (";var bLev=");
              s += batteryLevel;
              s += (";var dis=");
              s += distance;
              s += (";var kph=");
              s += motors.getSpeed();
              s += (";var movd=");
              s += motors.getTravel();
              s += (";var hed=");
              s += motors.getheading();
              s += (";</script></body></html>");
              h = F("HTTP/1.1 200 OK\r\nContent-Type: text/html\r\nConnection: Close\r\ncontent-length: ");
              h += s.length();
              h += F("\r\n\r\n");
              String ss = h + s;
			  server.sendContent(ss);
              yield();
              return;
}

void handleSounds(){
#ifdef Diag
  Serial.println("Handeling sounds");
#endif
  if(server.hasArg("Play")){
	  //String header = F("HTTP/1.1 301 OK\r\nCache-Control: no-cache\r\nConnection: Close\r\n\r\n");
		yield();
		server.sendContent(closeConnectionHeader);
		motors.play(server.arg("Play"));
  }else{
    sendFile(server.uri(),&server);
  }
}

void handleHeartBeat(){
		  pingOn = false;
          driverAssist = false;
          HeartBeatRcvd = true;
          server.sendContent(closeConnectionHeader);
          yield();
          return;
}

void handleRecievedPacket(){
	HeartBeatRcvd = true; // received data, must be connected
	if (autoMode) {
		autoMode = false; // disable autoMode if client sends packet
		HeartBeatRcvd = false;
		Stop();
	}
	motors.stopPlaying();
}

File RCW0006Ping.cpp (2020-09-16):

/*
Copyright 2017, Tilden Groves.

Licensed under the Apache License, Version 2.0 (the "License");
you may not use this file except in compliance with the License.
You may obtain a copy of the License at

    http://www.apache.org/licenses/LICENSE-2.0

Unless required by applicable law or agreed to in writing, software
distributed under the License is distributed on an "AS IS" BASIS,
WITHOUT WARRANTIES OR CONDITIONS OF ANY KIND, either express or implied.
See the License for the specific language governing permissions and
limitations under the License.
*/
/*
 * This is a non blocking ping library for the ESP8266.
 * 
 * The documentation recommends not pinging faster the 60ms to avoid echo's creating 
 * false readings
 *
 */
 
#include <ESP8266WiFi.h>
#include "RCW0006Ping.h"

#define TRIGGER D0                                            // Trigger pin
#define ECHO D8                                               // Echo Pin
volatile long pingTime;                                       // time taken to complete ping in uS
volatile int pingDistance = -1;                               // distance in mm
volatile int lastPingDistance = -1;                           // distance in mm

#define MAX_TEST_DISTANCE 4500                                // in mm
#define MAX_MEDIAN_SAMPLES 13                                 // use an odd number
volatile int currentMedianSample;
volatile int medianBuffer[MAX_MEDIAN_SAMPLES];
volatile int medianDistance = 500;
volatile int maxTimeNeeded = int((double(MAX_TEST_DISTANCE) / 10.0 * 58.0) / 1000.0);   // in ms
volatile long previousMillis = millis();                       // used for time out for no ping received
volatile int minimumDelay = 24;                                // to prevent false echo's
volatile long currentTimeout;

void pingSetup(){
  pinMode(TRIGGER, OUTPUT);
  pinMode(ECHO, INPUT);
  if (maxTimeNeeded < minimumDelay) maxTimeNeeded = minimumDelay;
  resetFilter();
}
ICACHE_RAM_ATTR void startup(){                                                 // ready now, wait for distance
  previousMillis = millis();
  pingTime = micros();
  detachInterrupt(ECHO);
  attachInterrupt(ECHO, calculateDistance, FALLING);
}
ICACHE_RAM_ATTR void calculateDistance(){
  unsigned long duration = micros() - pingTime - 5;             // added 50 uS to calibrate SQ4 sensor
  pingDistance = int((duration/2.0) / 2.91);                    // full equation int((duration/2.0) / 29.1 * 10.0);
  addToFilter(pingDistance);
}
void addToFilter(int pD){
  currentMedianSample++;
    for (int a = 0 ; a < MAX_MEDIAN_SAMPLES; a++){
        if (medianBuffer[a] < pD){
          for (int b = MAX_MEDIAN_SAMPLES - 1; b > a; b--){
            medianBuffer[b] = medianBuffer[b - 1];
          }
          medianBuffer[a] = pD;
          break;
        }
    }
    if (currentMedianSample == MAX_MEDIAN_SAMPLES){
      medianDistance = medianBuffer[int(MAX_MEDIAN_SAMPLES / 2.0)];
      resetFilter();
    }
}
void resetFilter(){
  for (int a =0 ; a < MAX_MEDIAN_SAMPLES; a++){
    medianBuffer[a]=-1;
  }
  currentMedianSample = 0;
}
int getMedian(){
  return medianDistance;
}
void triggerPing(){

  digitalWrite(TRIGGER, LOW);                                   // start low 2uS
  delayMicroseconds(2); 
  
  digitalWrite(TRIGGER, HIGH);                                  // datasheet states a uS 10  pulse to start
  delayMicroseconds(10); 
  
  digitalWrite(TRIGGER, LOW);   

  attachInterrupt(ECHO, startup, RISING);                       // when ready echo goes high
}

int getDistance(){                                              // returns distance or last distance or -1 if not available
  currentTimeout = millis() - previousMillis;
  if (pingDistance != -1 && currentTimeout > minimumDelay){
      lastPingDistance = pingDistance;                          // last real distance
      pingDistance = -1;
      triggerPing();
    }else if (currentTimeout > maxTimeNeeded){
      previousMillis = millis();                                // to stop false starts
      pingDistance = -1;
      triggerPing();
    }
    return lastPingDistance;
}

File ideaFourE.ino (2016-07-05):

//The initial sketch was based on the example provided by Sparkfun at;
//https://learn.sparkfun.com/tutorials/esp8266-thing-hookup-guide/example-sketch-ap-web-server
#include "library/ESP8266WiFi/src/ESP8266WiFi.h"
#include "library/DNSServer/src/DNSServer.h"
#include <Ticker.h>
#include "MotorController.h"

//////////////////////
// WebPage          //
//////////////////////
#include "WebPage.h"

extern "C" { 
   #include "user_interface.h" 
 } 


//////////////////////
// WiFi Definitions //
//////////////////////
const char WiFiAPPSK[] = "12345678";    // This is the Wifi Password
String AP_Name = "FH@Tbot";        // This is the Wifi Name(SSID), some numbers will be added for clarity
#define testCaptivePortal false

void setupWiFi(void);
void initHardware(void);

/////////////////////
// Pin Definitions //
/////////////////////
//const int LED_PIN = 16;      // The onboard LED
//const int ANALOG_PIN = A0;  // The analog pin 
//const int DIGITAL_PIN = 0;  // Digital pin to be read

//const int motorLeftA  = D2;
//const int motorLeftB  = D3;
//const int motorRightA = D4;
//const int motorRightB = D5;

const int motorLeftDir  = D2;
const int motorLeftSpd  = D3;
const int motorRightDir = D0;
const int motorRightSpd = D1;

motorController motors(motorLeftDir,D5,motorLeftSpd,motorRightDir,D4,motorRightSpd);

WiFiServer server(80); // http only https is 443
DNSServer dnsServer;
Ticker HeartBeatTicker;

bool HeartBeatRcvd = false;

void Stop(void)
{
  motors.update(0,0);
  //Serial.println("STOP");
}

void CheckHeartBeat(void)
{
  if (HeartBeatRcvd == true)
  {
    HeartBeatRcvd = false;
  }
  else
  {
    Stop();
 //   Serial.println("STOP!!!!!!");
  }
}

void setup()
{
  initHardware();
  setupWiFi();
  server.begin();
  HeartBeatTicker.attach_ms(500, CheckHeartBeat);
  Stop();
}

void loop()
{
   dnsServer.processNextRequest();
   WiFiClient client = server.available();
  if (!client)
  {
      return;
  }
  // Read the first line of the request
  String req = client.readStringUntil('\r');
  Serial.println(req);
  client.flush();

  if (req.indexOf("/X") != -1 && req.indexOf("/Y") != -1){
    String xOffset = req.substring(req.indexOf("/X")+2, req.indexOf("/X")+8);
    int dX = xOffset.toInt();
    Serial.print("DX: ");
    Serial.print(dX);

    String yOffset = req.substring(req.indexOf("/Y")+2, req.indexOf("/Y")+8);
    int dY = yOffset.toInt();
    Serial.print(F(" DY: "));
    Serial.println(dY);
    
    motors.update(dX,dY);
    
    Serial.print(F("Free Ram: "));
    Serial.println(system_get_free_heap_size());

    HeartBeatRcvd = true; // recieved data, must be connected
    client.abort();
  }else{
          client.write_P(HTML_text,strlen_P(HTML_text));
        }

   delay(1);
}

void setupWiFi()
{
  WiFi.mode(WIFI_AP);
 
  // Do a little work to get a unique-ish name. Append the
  // last two bytes of the MAC (HEX'd) to "FH@Tbot":
  uint8_t mac[WL_MAC_ADDR_LENGTH];
  WiFi.softAPmacAddress(mac);
  String macID = String(mac[WL_MAC_ADDR_LENGTH - 2], HEX) +
                 String(mac[WL_MAC_ADDR_LENGTH - 1], HEX);
  macID.toUpperCase();
  String AP_NameString = AP_Name + " " +macID;

  char AP_NameChar[AP_NameString.length() + 1];
  memset(AP_NameChar, 0, AP_NameString.length() + 1);

  for (int i = 0; i < AP_NameString.length(); i++)
    AP_NameChar[i] = AP_NameString.charAt(i);
  int channel = random(1,13);
  const byte DNS_PORT = 53;
  IPAddress subnet(255, 255, 255, 0);
  IPAddress apIP(192, 168, 1, 1);
  WiFi.softAPConfig(apIP, apIP, subnet);
  WiFi.softAP(AP_NameChar, WiFiAPPSK , channel , 0 );
   // set all traffic to 192.168.1.1 automatically
  dnsServer.setErrorReplyCode(DNSReplyCode::NoError);
  if (testCaptivePortal)
  dnsServer.start(DNS_PORT, "*", apIP);
}

void initHardware()
{
  Serial.begin(115200);
  delay(100);
  Serial.println("");
  Serial.println("FH@Tbot Serial Connected");
}

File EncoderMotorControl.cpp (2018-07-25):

/*
Copyright 2017, Tilden Groves.

Licensed under the Apache License, Version 2.0 (the "License");
you may not use this file except in compliance with the License.
You may obtain a copy of the License at

    http://www.apache.org/licenses/LICENSE-2.0

Unless required by applicable law or agreed to in writing, software
distributed under the License is distributed on an "AS IS" BASIS,
WITHOUT WARRANTIES OR CONDITIONS OF ANY KIND, either express or implied.
See the License for the specific language governing permissions and
limitations under the License.
*/

#include "EncoderMotorControl.h"
#include "fastIO.h"
extern "C"{
	#include "pwm.h"
	#include "user_interface.h"
}

encoderMotorController::encoderMotorController(uint8_t motorA_pin_1 , uint8_t motorA_pin_2 ,uint8_t motorB_pin_1 , uint8_t motorB_pin_2,uint8_t encoderA_pin_1,uint8_t encoderA_pin_2){
  motorAPin1 = motorA_pin_1;
  motorAPin2 = motorA_pin_2;
  motorBPin1 = motorB_pin_1;
  motorBPin2 = motorB_pin_2;
  pinMode(motorAPin1,OUTPUT);
  pinMode(motorAPin2,OUTPUT);
  pinMode(motorBPin1,OUTPUT);
  pinMode(motorBPin2,OUTPUT);
  digitalWrite(motorAPin1,LOW);
  digitalWrite(motorAPin2,LOW);
  digitalWrite(motorBPin1,LOW);
  digitalWrite(motorBPin2,LOW);
  lastX = 0;
  lastY = 0;
  for (int a = 0; a < 2; a++){
    lastSampleDeltaT[a] = 0;
    steps[a] = 0;
    totalSteps[a] = 0;
    lastMicros[a] = micros();
    wheelSpeed[a] = 0;
    motorDirection[a] = forward;
    timeOfFirstStep[a] = 0;
    timeOfLastStep[a] = 0;
    timeOfCurrentStep[a] = 0;
    wheelTargetSpeed[a] = 0;
    boostOn[a] = false;
    debounceMinStepTime[a] = (distancePerStep / (MAX_Speed/3600.0)) * 0.5;
    lastError[a] = 0;
  }
  //  initialize new PWM library
	uint32 pwm_duty_init[PWM_CHANNELS];
	for (uint8_t channel = 0; channel < PWM_CHANNELS; channel++) {
		pwm_duty_init[channel] = 0;
	}
	pwm_init(PWM_PERIOD, pwm_duty_init, PWM_CHANNELS, io_info);
	pwm_start();
}
 float encoderMotorController::checkNormal(float normal){
  if (normal > 1)normal = 1.0;
  if (normal < 0)normal = 0.0;
  return normal;
 }

 int encoderMotorController::makePositive(int number){
  if (number < 0){
    number = -number;
  }
  return number;
}
 double encoderMotorController::makePositive(double number){
  if (number < 0){
    number = -number;
  }
  return number;
}
void encoderMotorController::playNote(int note,double duration){
  if (note >= NOTE_B0){ 
  delay(1);
  double noteFrequency = 1.0 / note ;
  noteFrequency *= 1000000.00;
  double noteHalfDuration = noteFrequency * 0.5; 
  double a=0;
  while (a<(duration/(noteFrequency/1000.0))){
	a++;
	fastDigitalWrite(motorAPin1,0);
	fastDigitalWrite(motorAPin2,HIGH);
	fastDigitalWrite(motorBPin1,0);
	fastDigitalWrite(motorBPin2,HIGH);
	delayMicroseconds(noteHalfDuration);
	fastDigitalWrite(motorAPin1,HIGH);
	fastDigitalWrite(motorAPin2,0);
	fastDigitalWrite(motorBPin1,HIGH);
	fastDigitalWrite(motorBPin2,0);
	delayMicroseconds(noteHalfDuration);
  }
  pwm_set_duty(0, 0);
  pwm_set_duty(0, 1);
  pwm_set_duty(0, 2);
  pwm_set_duty(0, 3);
  pwm_start();
  delay(10);
  }else{
    delay(duration + 11);
  }
}
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

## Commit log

2016-07-11 Minor bug fixes, added minimum speed setting to avoid motor stall and tweaked DNS server now starts at "fhtbot.com" :)
    Minor bug fixes, added minimum speed setting to avoid motor stall and tweaked DNS server now starts at "fhtbot.com" :)
    [FH_Tbot.ino]
2016-07-13 Initial OpenScad commit
    Only a wheel so far
    [Fh@TBot.scad]
2016-07-13 Quick Tidy
    [Fh@TBot.scad]
2016-07-23 Added a compatibility mode for for older devices
    If compatibility is set to true radio will be set to 11b and no encryption
2016-08-04 updates and bug fixes
    Serial set to 9600 for compatibility with ping sensor.
    Removed blocking code in main loop to remove 80ms block per command from web browser.
    Added ping sensor library, connect RX to RX and TX to TX !.
    Improved but not fixed compatibility with chrome browser, hitting refresh every 30 seconds or so will get it to load :( .
    [FH_Tbot.ino]
2016-08-05 Added Neopixel Library
    Added Neopixel Library
    Changed Motor type and pin out
    Added Serial.swap() but probably need to test this
    [FH_Tbot.ino]
2016-08-16 Added new controller page
    A modified version of the virtual joystick based controller that uses buttons to send custom messages to the robot.
2016-08-28 started encoder library and some minor driver assist functions
2016-08-29 Added optional 'blinker' function that indicates Bot's direction of travel on forward LEDs. Note:untested
2016-08-30 Tested and fixed bugs to enable blinkers
    [FH_Tbot.ino]
2016-09-07 update to current build
2016-09-07 fixed bug where encoder steps where added in wrong direction while coasting to a stop.
    [FH_Tbot.ino]
2016-10-01 All drive functions roughed out
    Will now accept a get request with a drive data string EG.. data,F,40,R,90,
    All drive functions now accept target speed, target angle etc.
    Currently waddles like a duck due to PID still pending. However seems to drive ok.
    Still needs some serious tuning to get closer to targets.
2016-10-06 Improved speed readings and tightened up timing on debounce
    [EncoderMotorControl.cpp, EncoderMotorControl.h, FH_Tbot.ino]
2016-10-07 Bug Fixes & ....
    Speed control more accurate.
    Fixed bug in manual steering causing drift.
    Removed temperature information.
    Added new library functions for the new ping sensor using similar protocols to the SR-04 and US-100.
    Added unique heartbeats for each page so the ESP knows what page you are on.
    Speed control now using proportional feedback.....control is not bad... if I have time I'll add integral feedback too.
    [EncoderMotorControl.cpp, EncoderMotorControl.h, FH_Tbot.ino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]
2016-10-08 Removed last US-100 files
    RCW0006 functions now working D0 Trigger D8 Echo.
    Serial monitor set to 250000 for faster debugging.
    Type fixed on drive pages.
    [EncoderMotorControl.cpp, EncoderMotorControl.h, FH_Tbot.ino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]
2016-10-11 Minor modification to use an axel length of 88.8 with encoders on L>d7 R>d1. Remember to change if using a different pinout or axel width. Otherwise, remarkably accurate in turtle mode.
2016-10-12 Removed @ from most the files.
    Changed the background image name to background.png.
    Removed background image for readability from credits and about.
    Put temperature back on drive pages.
    Created place holder temperature function.
2016-10-13 added median filter ping + bug fixes
    [EncoderMotorControl.cpp, EncoderMotorControl.h, FH_Tbot.ino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]
2016-10-16 Added stop button and tooltips to blocks.
2016-10-17 Minor bug fixes and code tweeks
    [EncoderMotorControl.cpp, EncoderMotorControl.h, FH_Tbot.ino]
2016-10-20 Low power awareness and tweaks.
2016-10-20 Added missing files and fixed turtlemode path
    [EncoderMotorControl.cpp, EncoderMotorControl.h, FH_Tbot.ino]
2016-10-21 Added some more missing files from turtlemode
    [FH_Tbot.ino]
2016-10-22 updated ping settings for new sensor
2016-10-23 Bumpers now use interrupts
2016-10-24 Corrected stop button 404, added limiter, and changed background.
    Additionally tested feedback options for getting range and temperature. Range seems to freeze though.
2016-10-25 Update motor pins and Axle Length
2016-10-31 Tighten up avoidance turning in Assisted Drive mode.
    [FH_Tbot.ino, RCW0006Ping.cpp]
2016-11-06 Fixed incorrect notes in Imperial March theme.
    [EncoderMotorControl.cpp]
2016-11-06 Added missing function prototypes, fixed type mismatch in sendFile() prototype.
    [FH_Tbot.ino]
2016-11-09 Add files via upload
    Added PCB Gerber files
2016-11-09 Add files via upload
    Added stl model of wheel
    [Wheel.stl]
2016-11-09 Add files via upload
    Added dxf files of chassis
2016-11-09 Add files via upload
    Added BOM
    [FHTBot BOM.xlsx]
2017-01-16 Added Front of FHTBot with Etchings.
    This is the Corel draw file we used to cut th front of the robot. It has the "Face" etching included which is missing in the dxf files.
2017-01-31 inital socket implementation. However no connection yet.
2017-03-14 Wifi power reduced from 82 to 10, to be tested.
2017-03-14 Disconnect support and Socket Turtle added for websocket.
2017-07-20 Added manual start mode and 32 hole encoder
    Also some tweaks to manual drive mode
2017-07-27 ***Hardware change***
    updated battery pack to 6V
    added diode to prevent batterypack putting 6V on usb buss
    changed resistor on A0 to allow for battery voltage testing
    code now shows the current battery voltage in the temperature widget in drive mode
    [EncoderMotorControl.cpp, FH_Tbot.ino]
2017-07-28 Better Voltage display and stop motors incase of reset
    [EncoderMotorControl.cpp, FH_Tbot.ino]
2017-08-01 Revert "Merge branch 'master' of https://github.com/TildenG/FH_Tbot"
    This reverts commit 42244e47a5a961a9846a1fcdaa687b0058b8095c.
    [EncoderMotorControl.cpp, FH_Tbot.ino]
2017-08-04 Improved stability at low battery voltage
    Improved battery level display
    [EncoderMotorControl.cpp, EncoderMotorControl.h, FH_Tbot.ino]
2017-08-11 All PWM functions repliced by Stephan Bruens newPWM functions
2017-08-12 Tune PWM to 40 HZ
    minor code cleanup
2017-08-15 Syntax corrected after last compile fix.
    [FH_Tbot.ino]
2017-09-19 WS changes to fix early exit
    [FH_Tbot.ino]
2017-09-20 Added stl file for 3D printed wheel
    Tweaked to suit Up Min 3D printer
    [Wheel Up.stl]
2017-09-30 Minor changes to overcome compiler difficulty The compiler in windows versions of Arduino IDE seems to use a preprocessor that fixes a number of issues like missing '=' operators, but the linux versi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
    [EncoderMotorControl.h, FH_Tbot.ino]
2017-10-11 Fixed minor kick in turtle mode when changing direction
    slightly increase LED brightness on smile and drive mode
    increase bot maximum and reduce bot minimum speed
    [EncoderMotorControl.cpp, EncoderMotorControl.h, FH_Tbot.ino]
2017-10-11 Added Obstacle avoidance mode to main page
    [EncoderMotorControl.cpp, FH_Tbot.ino]
2017-10-13 Added a board tester to test new PCB's
2017-10-13 Moved board tester again
2017-10-14 Added missing prototypes
    tweek drive function
    [EncoderMotorControl.cpp, EncoderMotorControl.h, FH_Tbot.ino]
2017-10-18 Tweek board tester to work better with new led's
2017-10-19 Fix redirect
    tweek some motor settings
    [EncoderMotorControl.cpp, FH_Tbot.ino]
2017-10-23 Fixed error in #ifndef that disabled websockets
    [FH_Tbot.ino]
2017-10-24 Changed encoder wheel size to mk1 20 windows
2017-10-29 Minor fix to merge issue
    [EncoderMotorControl.h]
2017-10-30 Tiny tweek to alow small changes in steering speed
2017-11-09 Fixed some merge errors
    [EncoderMotorControl.h]
2018-06-06 Added PCB assembly drawings
2018-06-06 Create PCB Assembly Files
2018-07-25 Change core system to be compatible with the latest Board Files.
    Also. Make sound player non blocking.
    Changed some webpage names.
    [Wheel Up.stl]
2019-01-10 Fix compatibility issues with latest neopixel library
    [FH_Tbot.ino, FlashFiles.cpp]

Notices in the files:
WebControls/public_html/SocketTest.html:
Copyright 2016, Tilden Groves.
